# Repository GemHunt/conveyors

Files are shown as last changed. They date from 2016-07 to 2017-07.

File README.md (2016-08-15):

# Conveyors
Small laser cut conveyors

Check out the [assembly video](https://www.youtube.com/watch?v=6nuHHTepGgU) on YouTube.

See [Bill Of Materials](bill-of-materials/bill-of-materials.md) for pretty pictures.

[Laser Cutting Instructions](laser-cutting-instructions.md)

[Assembly Instructions](assembly-instructions.md)

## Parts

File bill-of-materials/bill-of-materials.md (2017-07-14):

**Conveyor Bill of Materials**

|Image | Name | Description | Source |
| --- | --- | --- | --- |
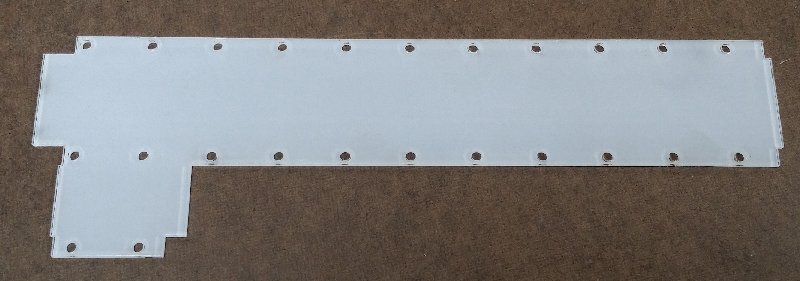
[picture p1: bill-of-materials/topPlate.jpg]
Top Plate
||Top Plate|Laser Cut 2mm clear acrylic sanded with 220 grit| Common |
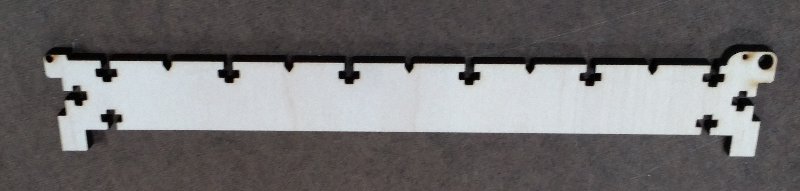
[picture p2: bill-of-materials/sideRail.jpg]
Side Rails
||Side Rails, Qty of 2|Laser Cut 6mm Baltic Birch Plywood| Most woodworker supply / hardwood stores have this|
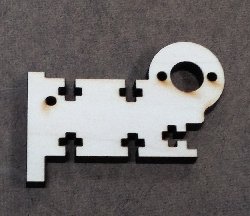
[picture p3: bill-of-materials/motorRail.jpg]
Motor Rail
||Motor Rail|Laser Cut 6mm Baltic Birch Plywood| " |
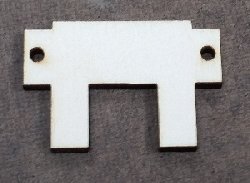
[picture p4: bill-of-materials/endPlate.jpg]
End Plate
||End Plate|Laser Cut 3mm Baltic Birch Plywood|"|
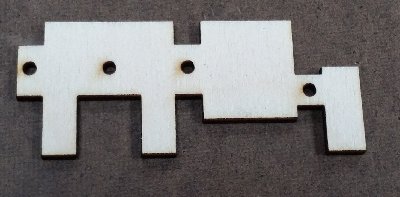
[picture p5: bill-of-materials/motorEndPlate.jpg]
Motor End Plate
||Motor End Plate|Laser Cut 3mm Baltic Birch Plywood| "|
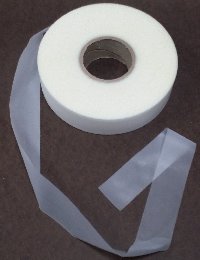
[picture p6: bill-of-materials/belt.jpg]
Belt
||Belt|0.15mm Thick 30mm wide 442mm long polyurethane | Search "TPU Tape" on AliExpress.com |
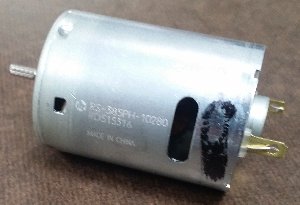
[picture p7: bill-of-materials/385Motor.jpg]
Motor
||Motor|24 volt DC motor (385) 3500RPM, 0.1 Amp | 2120461 at Jameco.com |
|No Picture|Motor|or 24 Volt 0.55 Amp 7.5 Step Angle Bipolar Stepper Motor | 2158557 at Jameco.com |
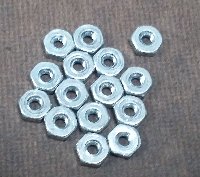
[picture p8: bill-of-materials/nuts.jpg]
Nuts
||Nuts| Standard 4-40 Nut, Qty of 15 | Common |
|Screws|Screws| 4-40 pan head screws 1/2"Qty 7 -- 3/8"qty 7 | Common |
|Motor Strews Motor Screws|Motor Screws| M2.6(.45mm) - 8 mm qty 2 | Hard to find!, Mcmaster-Carr, Aliexpress |
|Shafts|Shafts|42 and 60mm 2mm steel shafts | Common, Mcmaster-Carr, Aliexpress, Etc |
|Coupling|Shaft to motor Coupling|17mm long 1/16" ID 1/8" OD polyurethane tubing  | Mcmaster-Carr 	5549K43 |
|Bushings|Bushings|Two types right now. #2 nylon spacers, one 1/4" and two 1/2"  or 3/32" ID, Teflon  tubing 5/32" OD cut 29.5mm long | Mcmaster-Carr |
|Bearings|Bearings|Two 692zz 2x6x3mm bearings for the motor side shaft. You only need bushings or bearings. The nylon bushings are squeaky and only last like 200 hours. | AliExpress.com |
|Pulley|Pulley|Two types right now. #2 nylon spacer two 1/2" or Teflon tubing 3/32" ID, 5/32" OD, two cut 6mm long. These might have to on bearings as well...| Mcmaster-Carr |

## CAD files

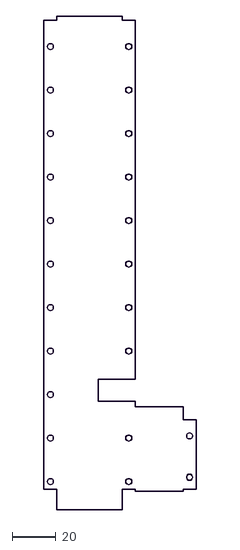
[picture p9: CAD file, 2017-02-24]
dxf-files/top-plate-solenoid-cut.dxf
70.0 x 227.0

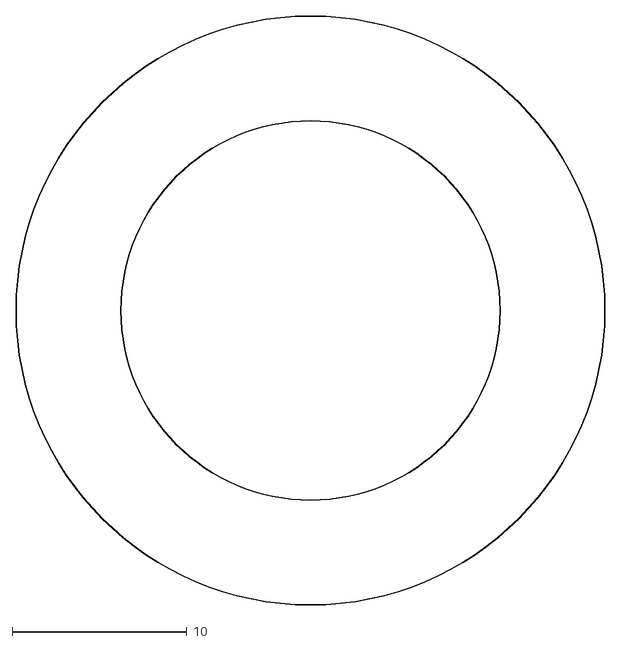
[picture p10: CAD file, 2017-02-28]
temp/6mm.dxf
33.7 x 33.7

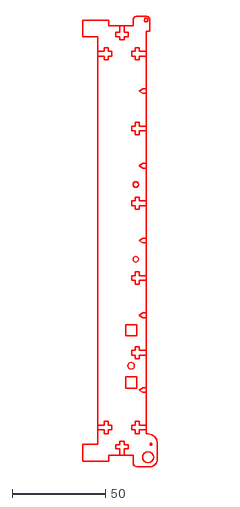
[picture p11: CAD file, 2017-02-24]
dxf-files/sideRail.dxf
40.0 x 241.0

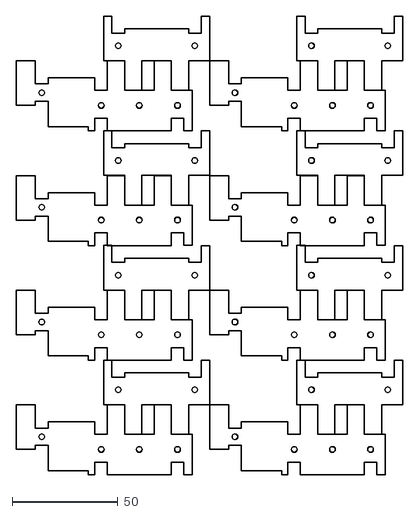
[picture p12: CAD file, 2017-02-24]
temp/3mm.dxf
182.2 x 216.4

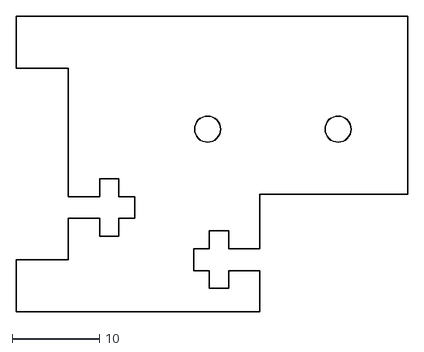
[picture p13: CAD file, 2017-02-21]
dxf-files/solenoid-plate.dxf
45.0 x 34.0

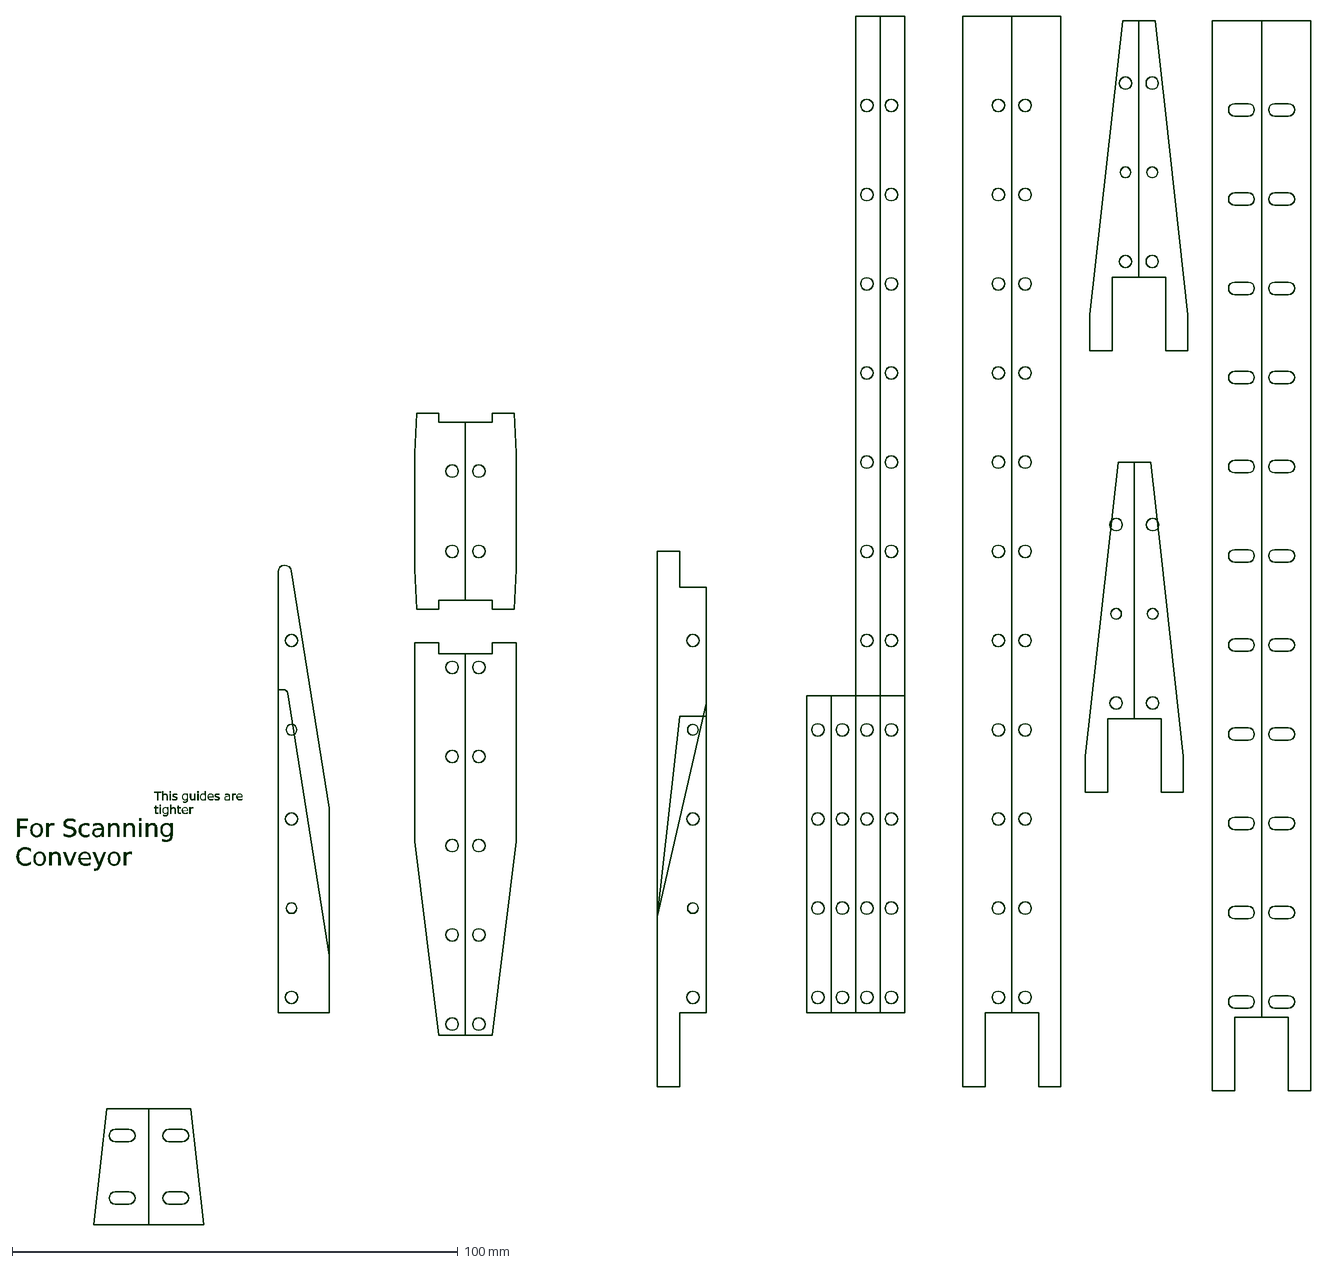
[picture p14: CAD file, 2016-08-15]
temp/miscGuides.dxf
This guides are tighter
For Scanning Conveyor

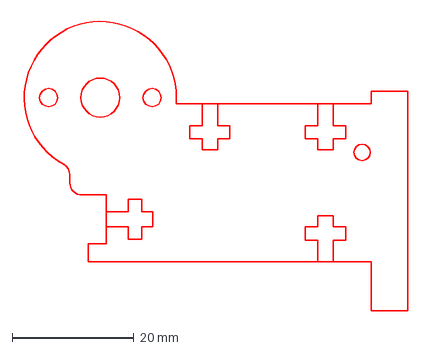
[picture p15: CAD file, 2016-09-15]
dxf-files/motor-rail-370-dc-motor.dxf
64.3 x 48.3 mm

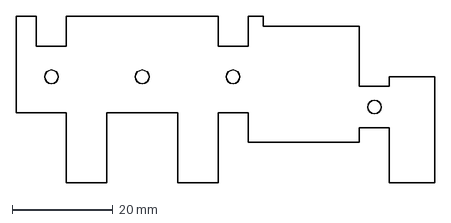
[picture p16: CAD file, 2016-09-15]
dxf-files/motor-end-plate.dxf
83.0 x 33.0 mm

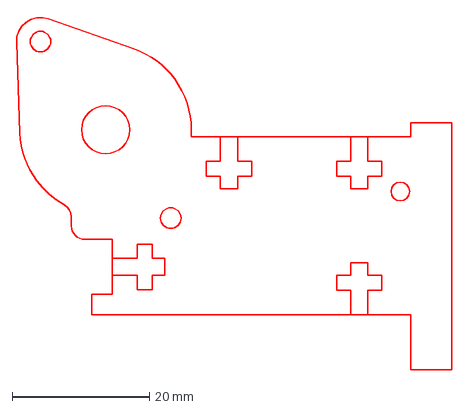
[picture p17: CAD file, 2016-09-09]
dxf-files/motor-rail-25by-stepper.dxf
63.5 x 51.6 mm

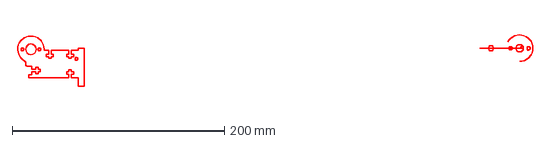
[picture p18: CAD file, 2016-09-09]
dxf-files/motor-rail-385-dc-motor.dxf
488.2 x 49.8 mm

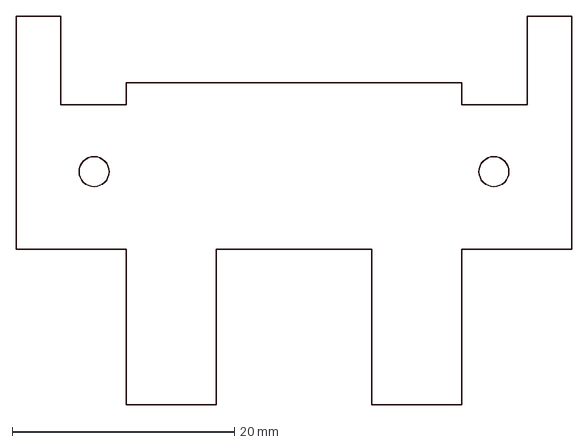
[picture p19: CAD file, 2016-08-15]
dxf-files/end-plate.dxf
50.0 x 35.0 mm

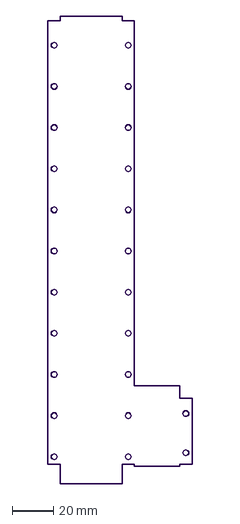
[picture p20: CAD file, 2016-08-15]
dxf-files/top-plate.dxf
70.0 x 227.0 mm

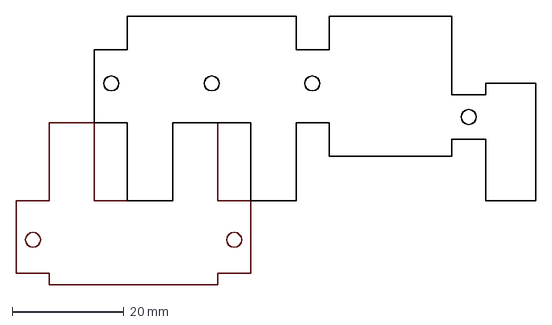
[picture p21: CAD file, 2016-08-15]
dxf-files/endPlates.dxf
93.0 x 48.0 mm

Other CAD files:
temp/3mm.3dm
temp/6mm.3dm
temp/endMount.3dm

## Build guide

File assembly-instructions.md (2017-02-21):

Conveyor Assembly Instructions

Assembly Tips:

Nuts go into the clean (non-charred) side better. 
If a nut gets stuck squeezing between 2 coins helps. 
370 Motors & solenoid have M3 8mm Long screws
385 Motors have an hard to find M2.6 x .45 size. 

All screws are 3/8” 4-40 unless you use guides. Use 1/2" Long screws with the guides. 

Only snug screws until everything it together, then finish tightening. 

Make a Belt:
The belts should be 95% the length of the distance between the motor shafts.
The glossy side should be the inside on the belt. The mat side is stickier. 
Cut 30mm wide belt:
	20cm Feeder/scanner Conveyor
	22cm short conveyor
	44.5cm hopper & accumulator conveyors
	104cm scanning conveyor

Heat seal (bond) smooth side in (Bright lighting helps)
I use an 8" $25 heat sealer for poly bags with a 2mm element.(3mm would be better)(A custom bonding rig would be nicer).
Scotch tape a 1mm overlap. 
Turn it inside out so the tape side is opposite the heating element before heat sealing. 
Heat seal 2 times to get the both side of the 1mm whole seam for .3mm thick
Heat seal 1 time for .15mm thick 
	On the dial I use a 2 setting for 0.15mm and 4.5 setting for 0.3mm
Remove Tape
Try not to heat seal a single layer area as this will thin it out. 
Clear belting is sticky. So sanding the top plate with 220 grit sandpaper is a must. It's a good idea regardless. 

Assembly Instructions:
	Add the 17mm coupling(tubing) to the motor
	Put the 60mm shaft on the other side of the couple
	There should be about a 1mm of tubing in the middle. 

Mount the motor	to the motor rail with:
	385 motor: M3x.5 x 8mm long screws.
	270? or 25mm gearmotors: M2.6 x 8mm long cap screws

Screw on top plate to motor rail
Add the solenoid plate, if there is one. 
Add a bearing to the motor shaft
Add Middle Rail to top plate with 2 screws

If using guides:	
Add them with three 5/8” screws instead of two ½” screws
Guides need shim washers between the top plate and the guide

Add the second side rail to top plate with 2 screws, adding the second bearing in the process

If using guides:	
Add them with three 5/8” screws instead of two ½” screws
Guides need shim washers between the top plate and the guide
Tighten guides with guide spacer in-between. 

Add shorter 42mm long 2mm shaft with 3/16 spacer pulleys:
	2 longer spacers on the end, and one shorter spacer in the middle. 
Put the belt on.

Add motor end plate
Add end plate

Final screw tightening:
Squeeze the side rails together when tightening the end plates. 
Don’t tighten top plate super tight as it will crown. 

Belt change:
Take off the end plates. 
Find a way to make it so you don’t have to take off the end plates? 
3 ½ minutes to change the belt with taking the end plates off. 
Squeeze the side rails together when tightening the end plates.

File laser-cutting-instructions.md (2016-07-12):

Conveyor Cutting Instructions

Laser Cutting Tips:

Push parts out from top (clean) side?

Instructions to Export to DXF from Rhino:
Rotating to top view is least confusing 
Mirror the side rail when cutting. 
Standard way to rotate to top views: 
	If you want to mirror flip the angle. 
If drawings are in Right view:
In front view, rotate, c    20, 0    90    enter - enter
If drawings are in Front view
In right view, rotate, c    0, 0    -90    enter - enter
Then invert & change object layer

Laser Cut 6 Parts:

6mm Plywood:
2 Side Rails
Motor Rail

3mm PlyWood:
End Plate
Motor End Plate

2mm Acrylic:
Top Plate
Laser Cut 6 Parts:

6mm Plywood:
2 Side Rails
Motor Rail

3mm PlyWood:
End Plate
Motor End Plate

2mm Acrylic:
Top Plate

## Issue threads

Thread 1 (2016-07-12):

Build a 4 conveyer Loop.

pkrush, 2016-07-12:
Build a 4 conveyer Loop

Issues so far:
Side Rails:
The 2mm shaft does not have enough wood around it.

pkrush, 2016-08-17:
Moved to a new repo and done.

Closed 2016-08-17.

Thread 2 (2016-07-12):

Slow the cube hopper to 1 coin a second.

pkrush, 2016-07-12:
@cdsupina:  You can lower the voltage on the Cube hopper to slow rate of coins coming out, but only to a point. Maybe you can get it down to 1-2 coins a second, but then it does not have the power to clear jams. We need to read the output line to detect when it dispenses a coin and turn the motor off briefly. This way we can slow the hopper to any rate we want.

pkrush, 2016-08-17:
Moved to a new Repo and done!

Closed 2016-08-17.

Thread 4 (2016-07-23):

Future Conveyor Ideas

pkrush, 2016-07-23:
**Conveyor Belt Bond in place tool:**
(Thanks @cdsupina) It would be nice to bond the belts in place when they get worn. The tool would have to clamp the ends so there would be no tension under the section that is being bonded. Flat NiChrome wire would do it, but would take a lot of amps at low voltages. Maybe the clamp can be thin steel with a resistive heater on it. I say steel, because it's poor conductor of heat, and you don't want the end of the clamp hot. I don't know. I did do this with a heat gun and aluminum in the past.

pkrush, 2016-07-28:
**Try Making Tiny Conveyors:**
How small can lasered T-Slot construction of the conveyors go?
* Try chamfered screws to hold the top plate. You would have to raster cut the top plate to allow the screw to be flush. *
* Try a 3mm side rails *
* Try powering belts with much smaller motors and a .1mm thick 6mm wide belt. *
* Try screwing into a slit instead of a nut and a T-slot. This is a way to miniaturize the conveyor, but you can have a skinny side rail. This would make it easier to assemble.  *

pkrush, 2016-07-28:
Try gluing the nuts in with a precise hot glue gun

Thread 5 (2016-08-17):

Run the 4 conveyor loop at least 1000 hours

pkrush, 2016-08-17:
I want this conveyor to run at least 1000 hours with no issues. A 1000 is not long, but you don't get much for $2 in parts!

So Nylon squeals after 30 hours and wears out after 200-300 hours.

Now 2 bearing have failed after 20-40 hours. I guess I need to find a cheap source and not a super cheap source!

pkrush, 2016-09-01:
Got new bearings from China. It's been working for 24 hours fine with 3 coins. I had to file one of the motor end plates...

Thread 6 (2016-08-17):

Misc updates

pkrush, 2016-08-17:
Change the Teflon pulley to 29mm long.  (Really this needs a replacement design...)
Go back to 58mm on the large shaft.
41mm on the short shaft
Change the motor rail to align the motor a bit better. You can see it’s just a little off.

pkrush, 2016-09-01:
Motor end plate:
Drop the  under the coupling as it was rubbing and raise it a bit around the bearings.

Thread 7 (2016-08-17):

Find a better drop off end bushing/bearing

pkrush, 2016-08-17:
Find a better drop off end bushing/bearing to replace the 29mm long Teflon tubing.

pkrush, 2016-09-15:
It's kind of funny as it does not seem to matter if it's wore out. Some bushings are not turning and the belt is sliding over them with no effort.

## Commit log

2016-07-11 Create conveyorBuildInstructions
2016-07-11 Update conveyorBuildInstructions
2016-07-12 Create conveyorCuttingInstructions
2016-07-12 Update conveyorAssemblyInstructions
2016-07-12 Update conveyorCuttingInstructions
2016-07-14 A bunch of guides from the past
    [miscGuides.dxf]
2016-07-14 Revise base plate
    Move non-motor track holes to the left on base plate
    [basePlateToConnect4InALoop.dxf]
2016-07-18 revise base plate
    add hole for motor plate
    [basePlateToConnect4InALoop.dxf]
2016-07-18 edit motor rail
    add t slot to motor rail
    [motorRail.dxf]
2016-07-18 redo in libreCAD
    [basePlateToConnect4InALoop.dxf, motorRail.dxf]
2016-08-03 Change to 692zz 2x6x3mm motor shaft bearings
2016-08-04 Make guides for lop of conveyors
    [guidesFor4InALoop.dxf, guidesFor4InALoopX4.dxf]
2016-08-04 make ir module, extra t-slot side rail
    [#topPlate.dxf, guidesFor4InALoopX4.dxf, ir_module.dxf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]
2016-08-04 hopper control arduino sketch
    [ir_module.dxf, sideRail_extra_tslots.dxf]
2016-08-15 Moving and renaming files
    [#topPlate.dxf, BeltTampener.dxf, basePlateToConnect4InALoop.dxf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]
2016-08-15 End plate changes to cover bearings
    [end-plate.dxf, motor-end-plate.dxf]
2016-08-15 Moved files to other repos
    [BeltTampener.dxf, guidesFor4InALoop.dxf, guidesFor4InALoopX4.dxf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]
2016-09-09 Cleaned up motor rail files and added stepper rail
    [motor-rail-25by-stepper.dxf, motor-rail-370-dc-motor.dxf, motor-rail-385-dc-motor.dxf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]
2016-09-09 Cap T Holes
    [motor-rail-25by-stepper.dxf]
2016-09-15 Fix of motor end plate touching the couping.
    [motor-end-plate.dxf, motor-rail-370-dc-motor.dxf]
2017-02-21 Updates for Camera
    [#topPlate.dxf, 2-conveyor-guide.dxf, 2-conveyor-top-plate.dxf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]
2017-02-23 clean up
    [2-conveyor-guide.dxf, 2-conveyor-top-plate.dxf]
2017-02-24 little updates
    [3mm.dxf, 6mm.dxf, sideRail.dxf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]
2017-02-27 Added Camera Parts
    [6mm.dxf, camera-cover.dxf, camera-top-rail.dxf]
2017-02-27 made symetrical
    [camera-cover.dxf]
2017-02-27 added camera-guides
    [camera-guides.dxf]
2017-02-28 added camera mount
    [camera-mounting-plate.dxf]
2017-03-03 Move to smaller clear guides
    [camera-guides.dxf]
2017-03-10 Moved Camera Mount to CoinSorter
    [camera-cover.dxf, camera-guide-washers.dxf, camera-guides.dxf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]
